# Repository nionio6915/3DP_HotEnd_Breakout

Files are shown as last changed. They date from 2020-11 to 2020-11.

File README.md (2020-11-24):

# 3DP_HotEnd_Breakout
PCB breakout board to tidy up the wiring at the hotend of a 3D Printer. <br>

Details: 
Traces on top & bottom.  
Hot End traces are estaimted to carry a maximum current of 5A at 2C temp rise.  <br>
This should in theory handle up to a 12v-50W heater using a 2-layer PCB with 1oz copper on each face.<br>   
Solder pads for SMT components are prortioned for hand soldeirng. SMT componnents are optional Pads are sized for 1206 sized components, but can be populated with as small as 0603's. <br>   

KiCAD generated .step file included for your convenience. <br>

Connectors provided for: <br>
E0 hot end, with screw terminals, same connector as on Duet2/3 hardware<br>
THERM themrmistor, JST XH / male header pins<br> 
FAN0: 1  hot end cooling fan, JST XH  / male header pins<br> 
FAN1: 2 part cooling fans, JST XH / male header pins<br>  
1 3-pin Z Probe connection <br>
1 2-pin LED connection<br>
1 2-pin AUX connection<br>  

LED's are optional. I like the convenience of seeing an indicator when observing my printer via webcam. I can not see the fans when they are running, so I added traces for indicator LED's. Similalry, not being abel to see the controller's LED's I added an indicator LED tied to the hotend and the LED circuit.<br>   

One addtional JST connector is provided in the event you are using a BL_Touch and require 5 conductors, 3+2. Else, the JST can be used for general purpose LED lighting of the carraige.<br>      

Male solder headers are shown, but thru-hole soldering of the wires directly to the board is prefered.<br>   

M3 screw holes are provided in the corners frou mounting, as well as 2 slotted holes for a zip-tie to secure the board/wires. <br> 

Board dimensions are approximteley 48mm x 24mm (1.87x0.93 inch)<br>  
As of 11/2020, $8.65 for 3 boards fabbed at OSHPark. <br>  

BOM:<br>   
5, 2-Pin JST XH_B2B-AM sockets  
    <https://octopart.com/b2b-xh-a%28lf%29%28sn%29-jst-7424860?r=sp>  
2, 3.5mm pitch screw terminal (Phoenix Contact 1751248) or equivalent  
    <https://octopart.com/search?q=Phoenix+Contact+1751248&currency=USD&specs=0>  
4, 0603 -1206 SMD Resistors, 760Ohm to 1KOhm  
    <https://octopart.com/search?q=0603+resistor&currency=USD&specs=0&resistance=1000>  
4, 0805 -1206 LED's of your choosing  
    <https://octopart.com/search?q=0805+LED&currency=USD&specs=0>  
6, 2 pin Male headers  
2, 3 pin Male headers  

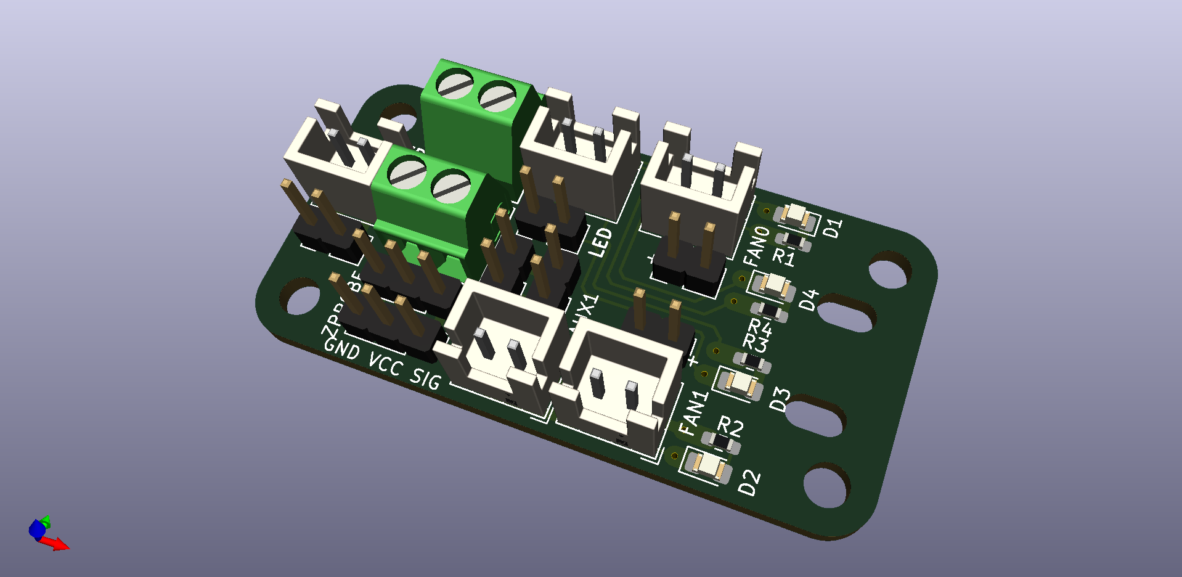
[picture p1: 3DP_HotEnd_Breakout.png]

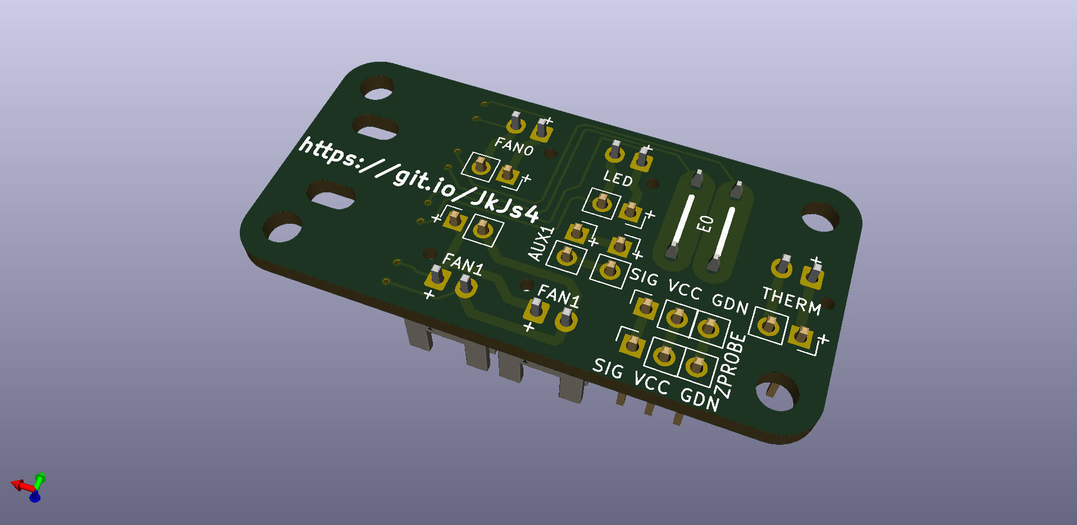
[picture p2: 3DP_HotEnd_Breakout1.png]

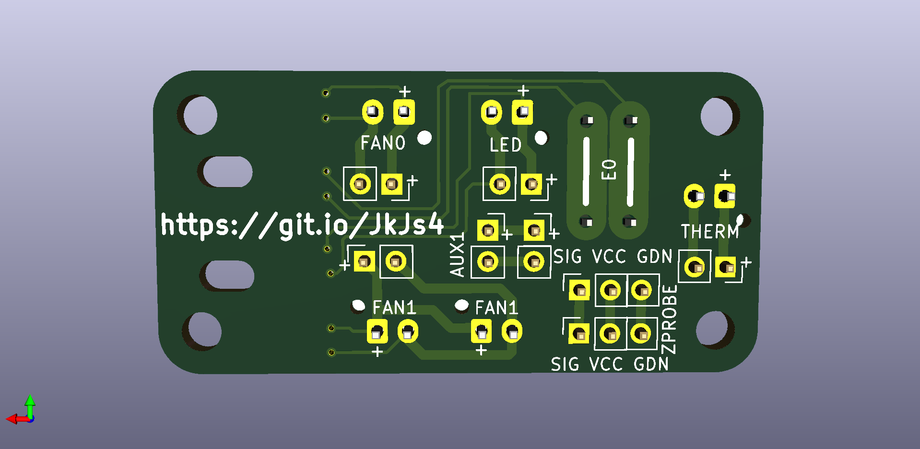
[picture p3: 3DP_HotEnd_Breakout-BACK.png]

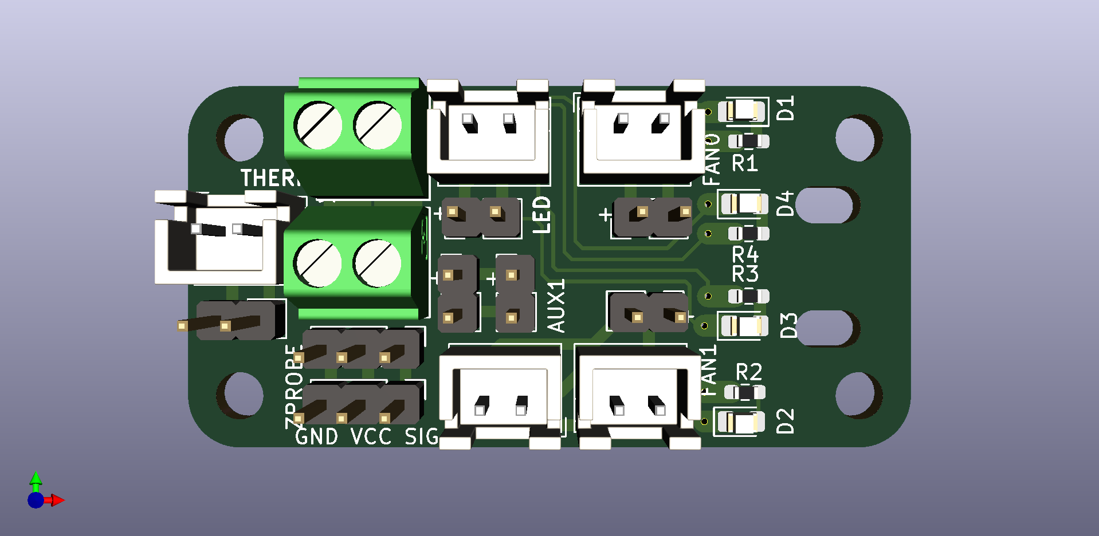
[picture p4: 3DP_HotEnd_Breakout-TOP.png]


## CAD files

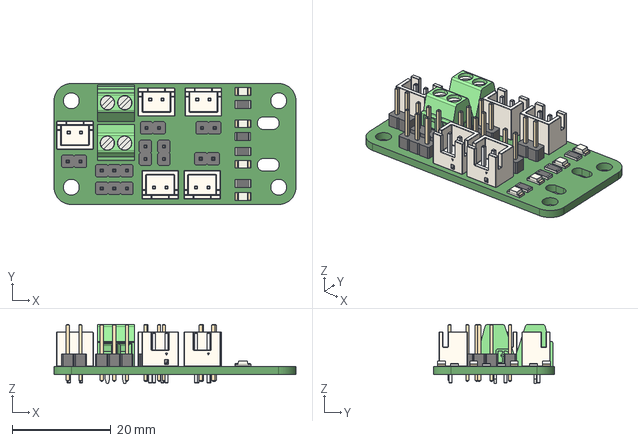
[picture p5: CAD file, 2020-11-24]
3DP_HotEnd_Breakout.step
49.0 x 24.5 x 12.0 mm

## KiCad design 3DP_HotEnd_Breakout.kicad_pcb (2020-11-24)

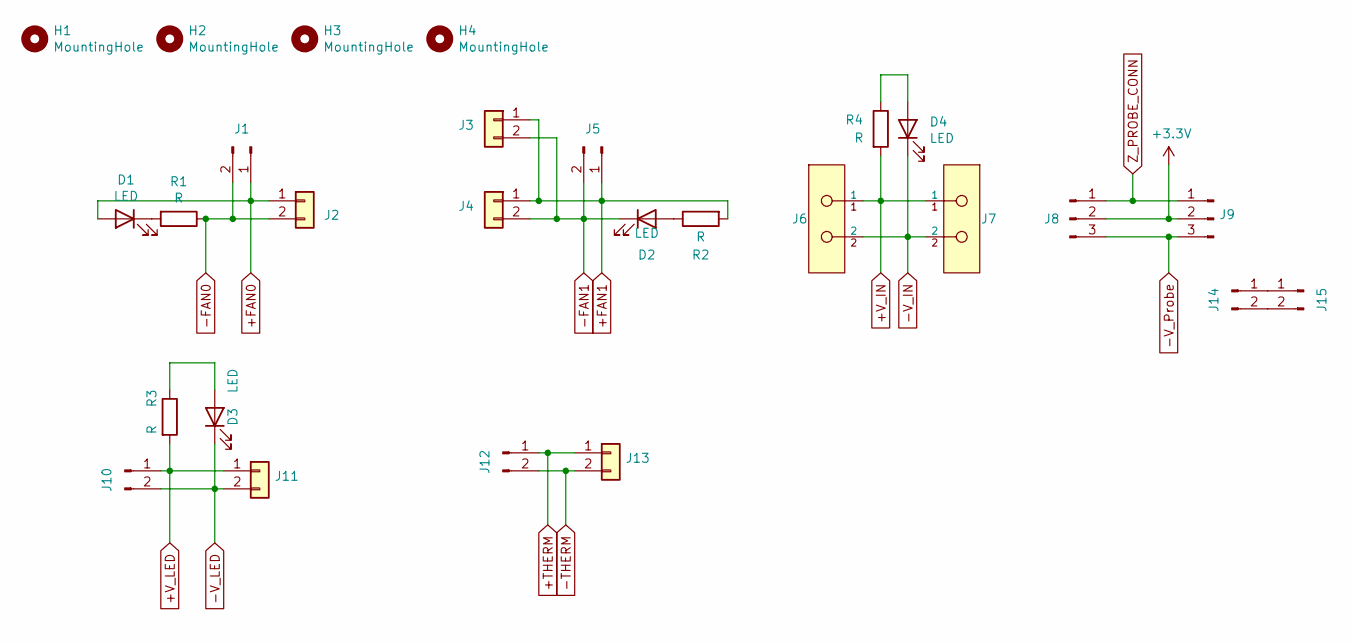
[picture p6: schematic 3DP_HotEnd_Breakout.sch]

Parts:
D1, D2, D3, D4: LED; LED_1206_3216Metric_Pad1.42x1.75mm_HandSolder
H1, H2, H3, H4: MountingHole; MountingHole_3.2mm_M3
J1, J5, J10, J12, J14, J15: Conn_01x02_Male; PinHeader_1x02_P2.54mm_Vertical
J2, J3, J4, J11, J13: Conn_01x02; JST_XH_B2B-XH-AM_1x02_P2.50mm_Vertical_DJP
J6, J7: 1751248; Phoenix_Contact-1751248-0-0-0; current rating 13.5A; voltage rating 200V; mouser part number 651-1751248; digikey description CONN TERM BLOCK 2POS 3.5MM
J8, J9: Conn_01x03_Male; PinHeader_1x03_P2.54mm_Vertical
R1, R2, R3, R4: R; R_1206_3216Metric_Pad1.30x1.75mm_HandSolder

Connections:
+3V3: J8.2, J9.2
+FAN0: D1.2 (A), J1.1, J2.1
+FAN1: J3.1, J4.1, J5.1, R2.2
+THERM: J12.1, J13.1
+V_IN: J6.1, J7.1, R4.2
+V_LED: J10.1, J11.1, R3.2
-FAN0: J1.2, J2.2, R1.1
-FAN1: D2.1 (K), J3.2, J4.2, J5.2
-THERM: J12.2, J13.2
-V_IN: D4.1 (K), J6.2, J7.2
-V_LED: D3.1 (K), J10.2, J11.2
-V_Probe: J8.3, J9.3
unnamed: D1.1 (K), R1.2
unnamed: D2.2 (A), R2.1
unnamed: D3.2 (A), R3.1
unnamed: D4.2 (A), R4.1
unnamed: J14.1, J15.1
unnamed: J14.2, J15.2
Z_PROBE_CONN: J8.1, J9.1

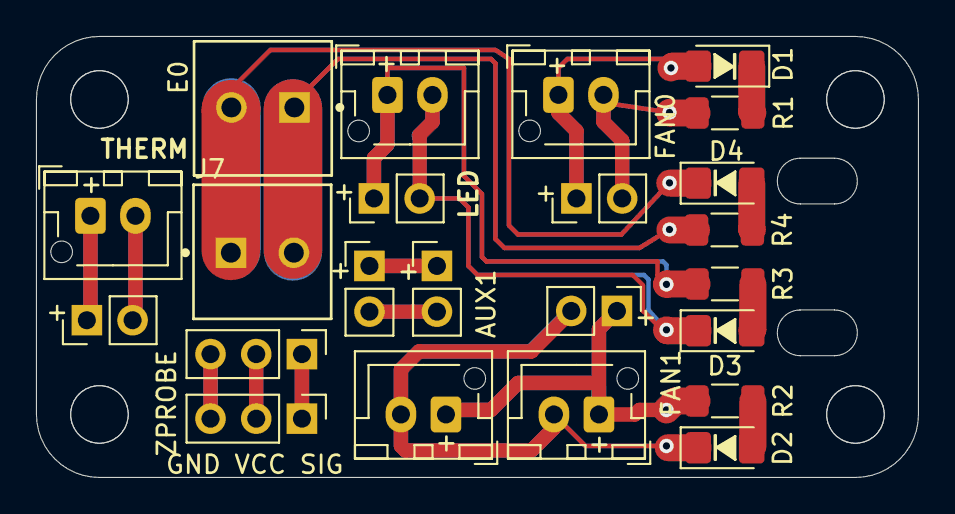
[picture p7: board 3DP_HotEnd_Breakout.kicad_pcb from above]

Board: 2 copper layers, 49.0 x 24.5 mm, 27 parts (0 on the bottom side), 19 nets.

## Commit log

2020-11-08 Initial Upload
    Initial Upload of PCB Design
    [CArraigeFanBreakout.kicad_pcb, CArraigeFanBreakout.sch]
2020-11-09 Initial commit
    Initial commit
    [3DP_HotEnd_Breakout-B_CrtYd.gbr, 3DP_HotEnd_Breakout-B_Cu.gbr, 3DP_HotEnd_Breakout-B_SilkS.gbr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]
2020-11-09 Fix jumper label alignements
    Fix jumper label alignements
    [3DP_HotEnd_Breakout-B_CrtYd.gbr, 3DP_HotEnd_Breakout-B_Cu.gbr, 3DP_HotEnd_Breakout-B_SilkS.gbr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]
2020-11-09 updated BOM & Details
    [3DP_HotEnd_Breakout.kicad_pcb]
2020-11-24 revised SMT pads
    [3DP_HotEnd_Breakout-B_CrtYd.gbr, 3DP_HotEnd_Breakout-B_Cu.gbr, 3DP_HotEnd_Breakout-B_SilkS.gbr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]
